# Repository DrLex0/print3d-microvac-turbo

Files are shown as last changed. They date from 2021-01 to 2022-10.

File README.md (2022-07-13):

# MicroVac Turbo
*A small (experimental) 3D printed handheld vacuum cleaner made from scrap parts*

### License
[Creative Commons - Attribution](https://creativecommons.org/licenses/by/4.0/)

### Gallery

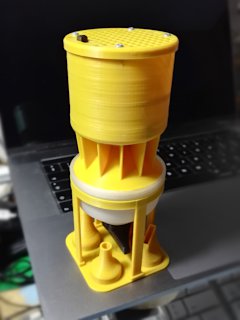
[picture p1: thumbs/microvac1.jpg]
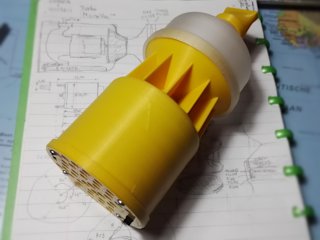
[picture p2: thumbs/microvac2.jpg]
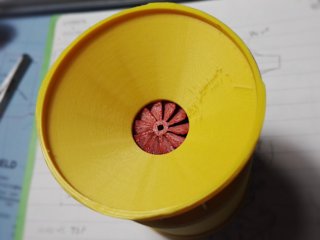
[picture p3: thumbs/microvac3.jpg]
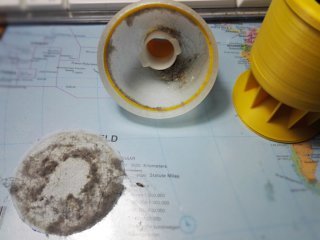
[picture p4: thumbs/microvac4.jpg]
Dirt
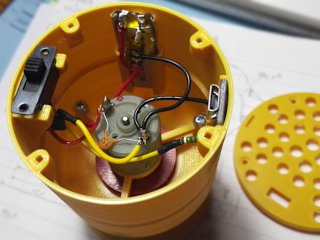
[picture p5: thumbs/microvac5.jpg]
Internals
[🔎](images/microvac1.jpg) [🔎](images/microvac2.jpg) [🔎](images/microvac3.jpg) [🔎](images/microvac4.jpg) [🔎](images/microvac5.jpg)

## Description and Instructions

This is a small (about 60 mm diameter and 150 mm tall) handheld vacuum cleaner that I basically made from scrap parts. It is more like a proof-of-concept and was designed to fit the parts I had, not to use commonly available components. It is unlikely you will be able to print and build this without first modifying the 3D models, because the motor I used may not be easy to find, and the LiPo battery I used certainly is not easy to find.

This mini vacuum cleaner is built around a turbo style impeller, just because I wanted to see how well it would work (pretty well apparently). After trying out a few impeller designs from other people, I created my own. This was done purely by eyeballing and wet-finger guessing, it probably isn't the most efficient design possible but it works pretty well for this application.

The vacuum cleaner itself is a very basic design, no fancy cyclones (if there is cyclone action, it would be by accident), just a widening collector to slow down the air and provide a relatively large filter area. I didn't expect much of it but it works surprisingly well and is useful for cleaning keyboards or electronic devices and hard to reach corners. It isn't ideal to suck up a lot of fluffy or very fine dust because this quickly clogs the filter, but it is great to quickly get rid of small pieces of junk. When sanding or carving something, I no longer care about the mess I make, I just vacuum it afterwards. It's also useful to clean the inside of a confined space like a 3D printer enclosure. This is one of the most useful 3D prints I have made so far.

Note: there is no relation between this freely available 3D printable model and any products or brands that may use the MicroVac name. This model is not condoned or endorsed by any company.

### Parts

IIRC the motor I used came from SparkFun long ago and they no longer sell this model at the time of this writing. The specifications were:
- 1.5V to 4.5V,
- 8400 rpm at 1.5V, 230 mA
- 14200 rpm at 3V, 280 mA
- 2 mm axle diameter
- Overall diameter: 20.75 mm, front diameter (around axle) 15.90 mm
- Coil impedance around 1 Ω

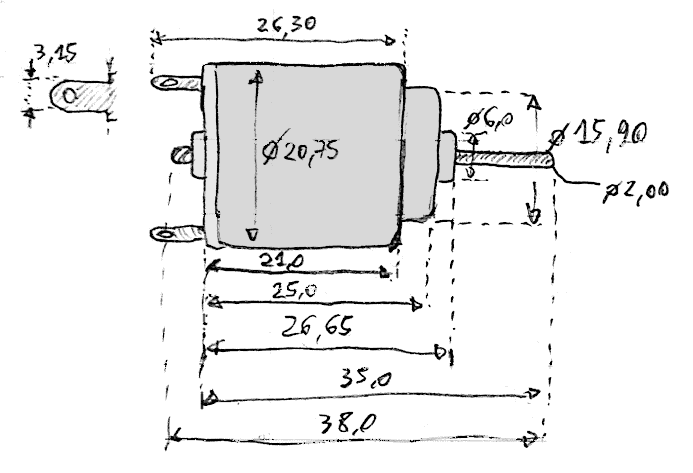
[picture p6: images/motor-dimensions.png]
Motor dimensions


It looks like this motor is a clone of the Mabuchi *RE-140RA.* You can get these clones from the usual sources like AliExpress. Those who live in Europe, the Reely R140 motor sold by Conrad (article 518398) is a perfect match.

My first motor endured almost 2 years of quite intensive use before its brushes were completely gone. Two things probably contributed to wear:
1. I hadn't sealed any of the holes in the housing, hence fine dust that got past my crude filter could enter the motor;
2. I added some oil to the bearings at regular intervals, to combat noise that was probably caused by the fine dust grinding away the bearings. I mostly added oil at the rear, because this was easily accessible (and actually also most prone to wear and causing noise). The oil mixed with the dust and became a grinding paste that lodged itself between the brushes and commutator, eventually destroying the brushes.

Learning from the above, the lifespan of the motor can probably be greatly improved by sealing all holes in the motor housing, and only applying minimal amounts of oil or (preferably) grease. Minimising vibrations by balancing the impeller will also help.\
I doubt whether genuine Mabuchis would last much longer. It makes sense to simply buy a stockpile of whatever you can get cheaply. Replacing the motor is easy, especially when using pluggable contacts.

Any motor with roughly similar specs and dimensions should be suitable. Pay attention to the RPM and current ratings. Lower values will not work well. Even if the free-air RPM matches, a motor with lower current draw will be too slow when it experiences the load of having to drive the impeller. After my original motor was beyond repair, I tried a purported Mabuchi (bought via AliExpress, so likely a fake) but it had a higher impedance on its coils and could not draw the same current, which made it too slow. I managed to transplant the rotor of the original motor into this new motor's housing and this works OK, although the commutator will probably fail next and then I will have to find a better replacement after all.

If you use a different model of motor, you will need to model your own motor mount. It may be a good idea to try a *drone motor* which will certainly be able to displace a lot of air. However, keep in mind that there will be an upper limit to the speed you can drive the impeller before it explodes into bits. Make sure to wear eye protection if you plan to find this speed limit… Also consider that the impeller will tend to spin faster inside the enclosure than in free air, especially when the inlet is obstructed.

The battery I used is a 220 mAh 551240 LiPo which came from a Chinese ‘spy pen’ gadget, the one [I reviewed here](https://www.dr-lex.be/hardware/spypen_review.html). After the protection circuit of this battery failed, I tried to find a replacement and this proved very difficult. This bare battery remained in my stockpile of loose parts until I decided to use it for this project, with a basic protection circuit attached to it. In other words, you will likely need to adapt the 3D model to fit a battery you can easily obtain. A slightly higher capacity than 220 mAh may be recommended although autonomy is pretty decent even with this small value. A bigger battery would also allow more current draw, hence better performance. You will of course need to modify the 3D model to allow mounting a different shape of battery.

The switch is a pretty standard 2P2T slide switch, a classic model that has been around for ages and should still be easy to find. I connected the two arrays of contacts together because the currents it has to deal with may be a little higher than it is intended for. So far, no problems whatsoever.

For the USB socket. I used a simple microUSB break-out board that is easy to find on AliExpress and the like, the dimensions are 14.1x12.7 mm. Of course you could use any other connector, USB-C if you want to be fancy. You could also look for a combination charge/discharge protection board that does everything to keep the battery in good shape and offers an indicator light.

The screws I used are simple self-tapping screws, 3 larger screws that hold the parts of the main body and the motor mount together are 2.9 mm × 9 mm; and 4 smaller screws for the lid are 2.2 mm × 6.5 mm. Anything similar will probably work, you could adjust the models if need be.

You also need some kind of *filter.* The 3D printed ‘filter’ is insufficient, its only purpose is to hold the actual finer filter in place. The filter should be a circle with 60 mm diameter, and it should be the thinnest possible material that still blocks fine dust. I simply peel and cut one layer from soft multi-ply toilet paper, which works very well.

### Printing

The recommended layer height for nearly all parts is 0.2 mm. Only the impeller should be printed at 0.1 mm layers with an extrusion width of 0.4 mm. For the other parts I recommend an extrusion width of 0.6 mm, which will be beneficial for strength. Since all parts are basically shells, infill doesn't really matter and safest is to use 100%.

I used PLA for all parts except the filter ring (see below) and the impeller, which is ABS. The only real reason for this is that I'm able to produce more detailed prints with ABS. Use whatever works best for you.

It is highly recommended to print the `FilterRing` in an *elastic filament* like TPU. Otherwise there may be a considerable air leak around the filter edges. Whether you need **one** or **two** of these filter rings, depends on how flat and smooth you can make the interface between the `CenterPart` and `Filter` parts. If it is perfectly flat, this interface will offer a good enough seal on its own, otherwise an extra gasket is recommended. In my case the surfaces are perfect because I print on a glass bed, but an alternative is to sand and polish these two surfaces.

The impeller is provided in both `clockwise` and `countercw` (counter-clockwise) variants. Which one you need, depends on the direction the axle of your motor turns when viewed from the front. The motors I have tried, all turn clockwise when connected with their indicated polarity. You could of course just swap the wires if you printed the wrong version, although I'm not sure whether some motors aren't optimised to run in a certain direction.\
There are 2 versions of the impeller, the `v2` version has blades of alternating height. It is hard to test this quantitatively, but in practice it appears to perform better.

There are two lid designs, `cheese` has a pattern with round holes, `grid` is a regular grid and in theory offers slightly better airflow.

Several mouthpiece styles are available. The most useful ones proved to be 3, 4, 5, and 6. These are press-fit, which means you might need to experiment a bit with scale factors to get a good fit. In my case, I have to scale these pieces to 99.5% in the XY plane to get a good fit. I printed the number 4 and 6 pieces in flexible PLA to reduce the risk of scratching things.

A stand is also provided that can hold up to 4 mouthpieces besides the vac itself. When printed well, the two parts will fit and hold together when pushed into each other, otherwise sandpaper and/or glue are your friends.

### Assembly

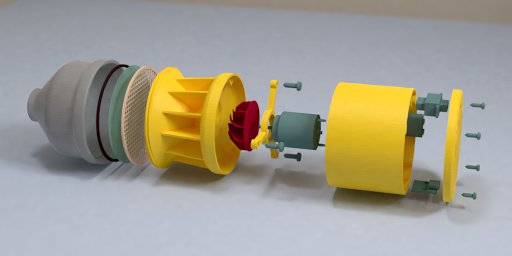
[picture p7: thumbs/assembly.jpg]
Exploded view
[🔎](images/assembly.jpg)

Assembly is rather straightforward. You should start by pushing the motor into its mount (it's press-fit) and then mounting the impeller. Tune the position of the impeller on the axle such that it just does not scrape against the intake part, also not when the airflow is blocked and the motor spins at its highest speed. I have created a spacer out of cardboard, fine-tuned with layers of adhesive tape through trial-and-error, such that I can simply push the impeller on the axle with the ideal spacing right away. When this is OK, assemble the other parts.

Cut a fine 60 mm diameter filter out of some thin material, like a single ply of soft toilet paper. You can use the coarse filter as a template. Place this thin filter on top of the coarse filter, preferably at the top side where the grid is slightly recessed. Then place the flexible ring on top of the fine filter and align everything. While keeping the set of filters in this orientation, insert them into the collector with its outlet pointing upwards. If you decided to use two flexible rings, place the second ring onto the coarse filter. Then screw the collector onto the main body of the vacuum cleaner.

The inlet has a tab on the side, the idea was to stick a piece of paper or plastic sheet to it, to act as a valve. This has proven unnecessary though when emptying the collector regularly. Junk will typically move to the sides and not fall back into the inlet unless too much has been collected.

Due to imperfections of the 3D printing process, the impeller may be unbalanced enough that it causes annoying vibrations. Balancing the impeller is fairly easy: mount it on a perfectly straight 2 mm rod (like a drill bit), and let the axle roll on 2 ‘rails’ that are perfectly level and flat. If well balanced, the impeller should not seek out a specific orientation when nudged. If it does, first look for obvious blobs at the side that likes to point downwards, and remove them. If this does not suffice, stick some adhesive tape at the edge that likes to point upwards, and try to dose it such that the impeller no longer has any preferred position. Enjoy your vibration-free MicroVac!

#### Wiring

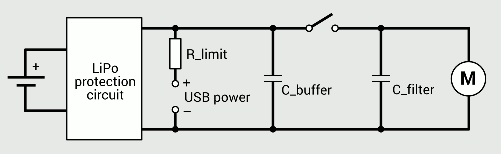
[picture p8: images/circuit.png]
circuit


How to wire this thing will depend on the specific parts used, but in general it is rather straightforward. One wire of the motor goes to common ground, the other goes through a switch to the positive terminal of the battery protection circuit. The positive terminal of the battery's over-voltage protection circuit goes to a charging port. Ideally there should also be a current regulator to limit the current during charging. Usually, a good rule of thumb for the charge current is the same milli-amperes value as the battery's capacity in mAh (or “1 C”). In my case, the current limiter is extremely simple: a resistor chosen such that the peak current is not much higher than 1 C. This is inefficient, but OK given the small capacity of the battery I'm using and the low current it charges at. For a higher capacity battery, you will want to use some active charging circuit, because a resistor could become dangerously hot.

There are some ready-to-use boards that have a microUSB (or nowadays USB-C) port with charge and protection circuit all-in, but you will need to modify the 3D models to fit those.

If you cannot find a motor that runs at a good speed between 3.8 and 4.2 V, you will have to add some kind of booster circuit, or use 2 batteries with possibly a step-down circuit.

Refinements that are good practice: ensure there is a small ceramic capacitor as close to the motor terminals as possible, to filter out noise (may not be needed depending on the type of motor). Also, a decently sized capacitor across the battery (I used 470 nF), to buffer the initial inrush current when switching on the motor. This should also be placed as near to the motor as possible but must come before the switch. Without this capacitor, the protection circuit of my battery would sometimes engage because the inrush current could be high enough for the protection circuit to consider it a short-circuit.

Using crimp terminals for the motor will make it easier to replace than when soldering it. The RE-140RA and clones have tabs that accept plain flat 2.8 mm terminal connectors. Ideally the connectors should be for 0.3 mm thick tabs but if hard to find, 0.5 mm connectors will also work after some careful squishing.

### Using

There isn't much to say about how to vacuum things, just turn it on and go for it. If you didn't make a valve to keep dirt inside, the only thing you should avoid is wildly shaking the device or allowing it to fill up to a point where dirt can no longer stay inside.

Depending on your wiring, you may be able to get an extra boost by connecting the USB cable. In my case the gain is minimal due to the rather high impedance of my barebones current limiter. Make sure you cannot send the motor into explosive overdrive when it receives 5 V instead of the usual 4.2 V maximum of a LiPo battery.

To empty the reservoir, unscrew the collector from the rest, obviously while keeping it upright. Then either take out the filters using tweezers, or just immediately topple the whole thing over above a dustbin, catching the filters with your hand. If you're careful, you can shake the fine filter and reuse it, but the effort to make new filters is pretty small anyway. Afterwards, reassemble according to the above instructions.

The mounting/removing of the filters and the screw thread connection to mount the collector aren't very user-friendly, but this was only a proof-of-concept after all.

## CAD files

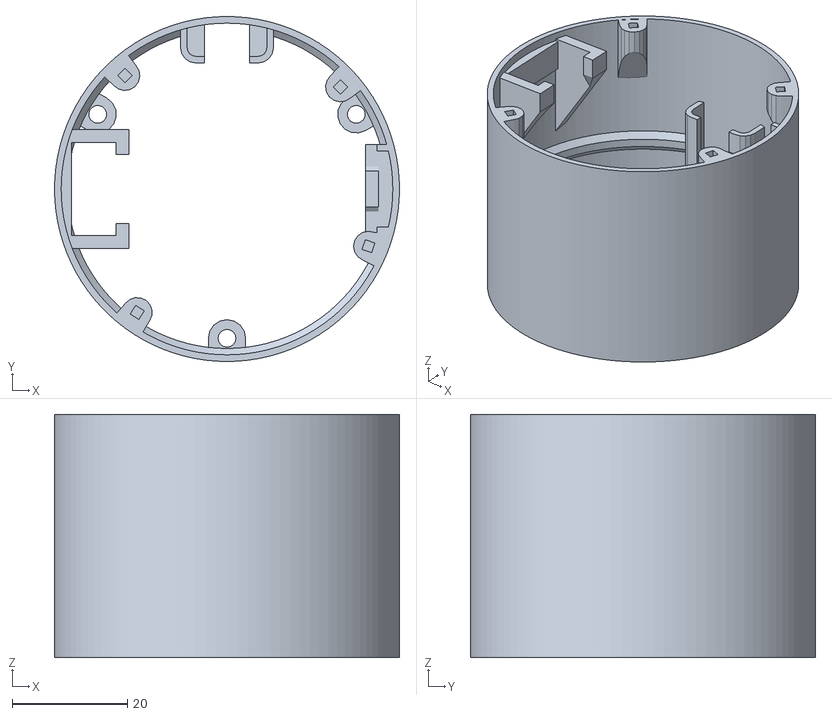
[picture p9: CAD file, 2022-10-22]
stl_files/UpperPart.stl
60.0 x 60.0 x 42.3

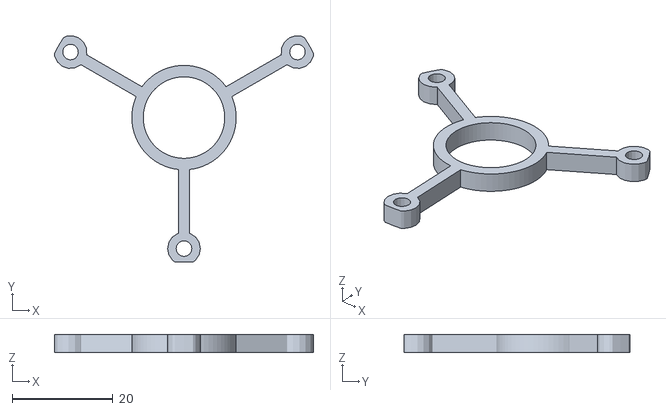
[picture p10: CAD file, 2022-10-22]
stl_files/MotorMount.stl
51.3 x 44.9 x 3.60

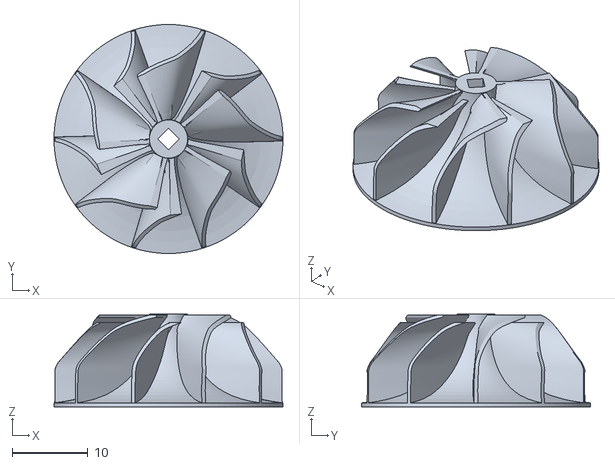
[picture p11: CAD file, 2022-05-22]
stl_files/Impeller-v2-countercw.stl
30.2 x 30.2 x 12.2

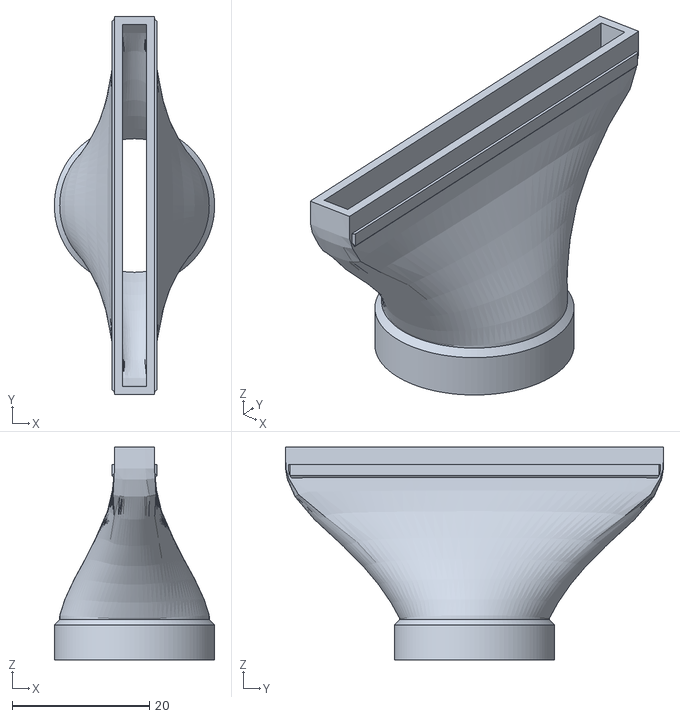
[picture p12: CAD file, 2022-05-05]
stl_files/Mouthpiece6.stl
23.3 x 55.0 x 30.9

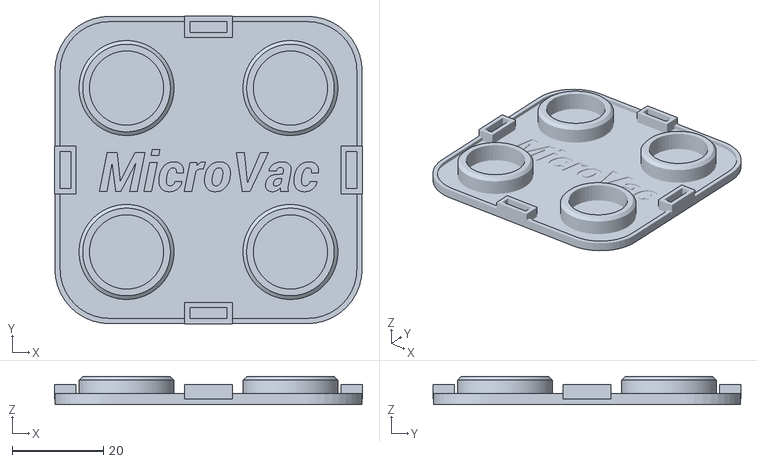
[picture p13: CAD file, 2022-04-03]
stl_files/Stand-lower.stl
67.6 x 67.6 x 6.20

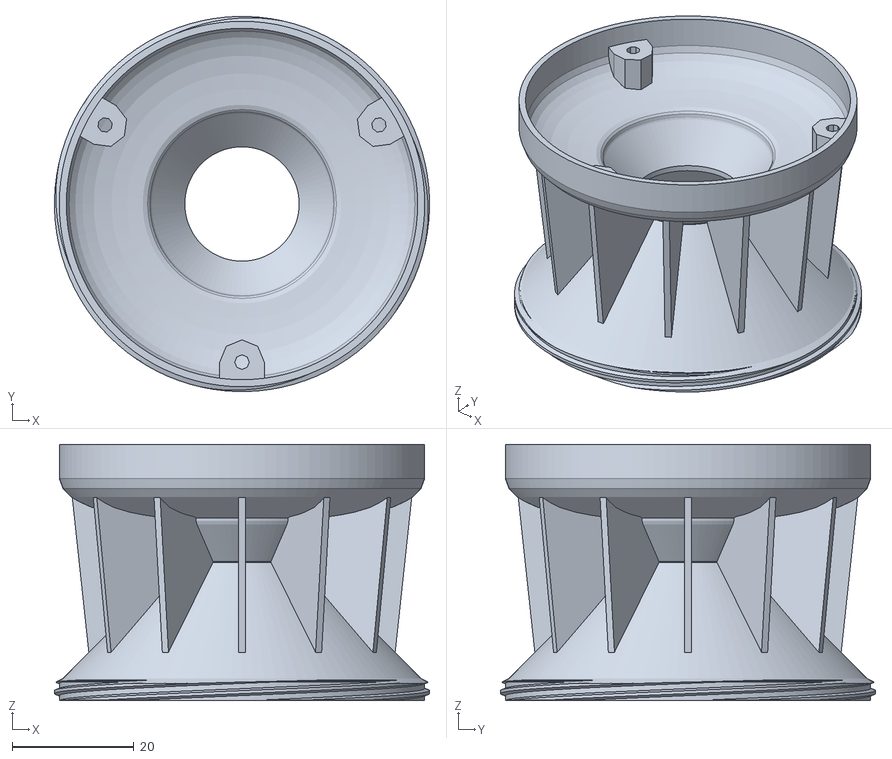
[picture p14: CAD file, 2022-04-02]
stl_files/CenterPart.stl
61.6 x 61.6 x 42.0

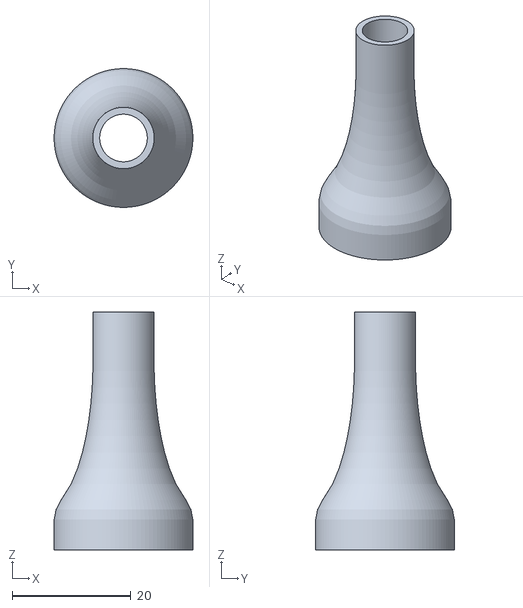
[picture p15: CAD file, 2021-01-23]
stl_files/Mouthpiece5.stl
23.3 x 23.3 x 40.0

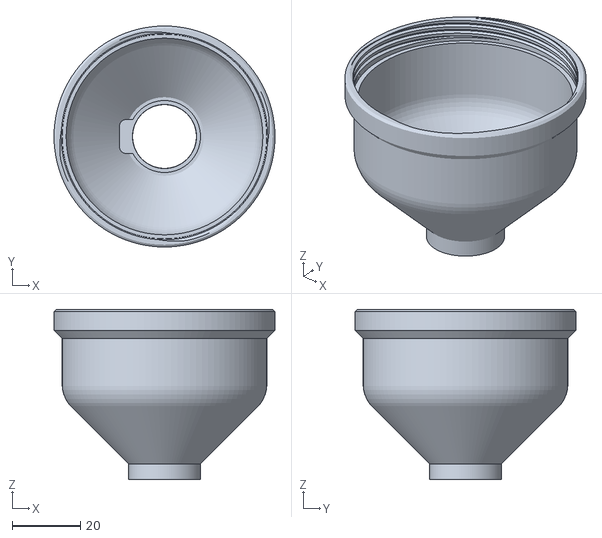
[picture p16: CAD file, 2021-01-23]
stl_files/Collector.stl
64.8 x 64.8 x 49.9

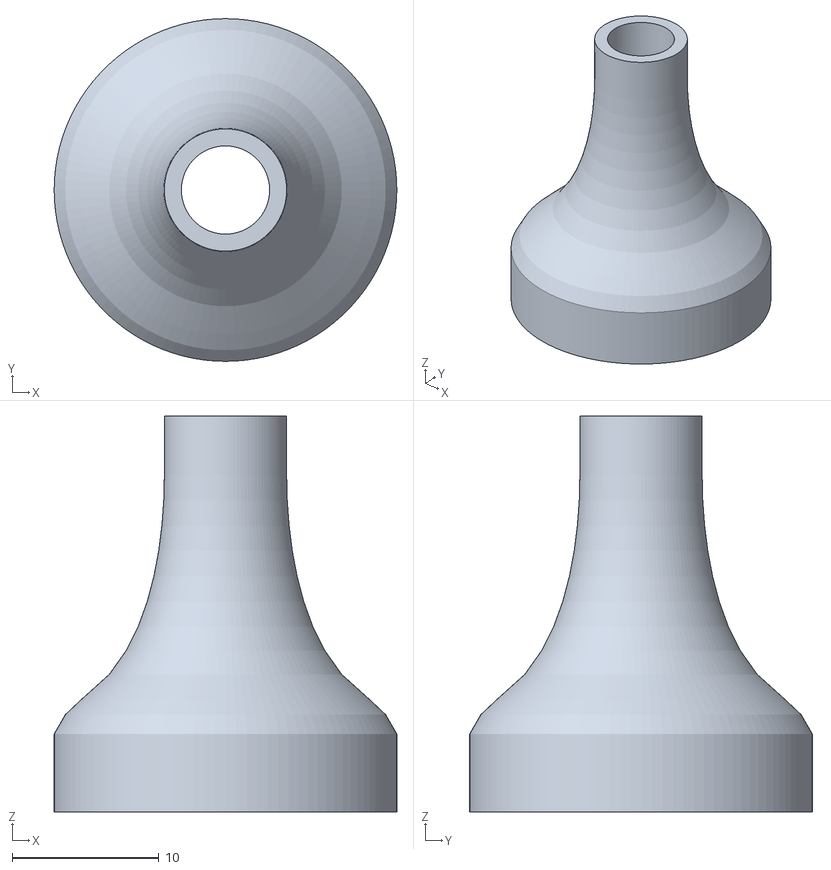
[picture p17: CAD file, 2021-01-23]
stl_files/Mouthpiece3.stl
23.3 x 23.3 x 26.9

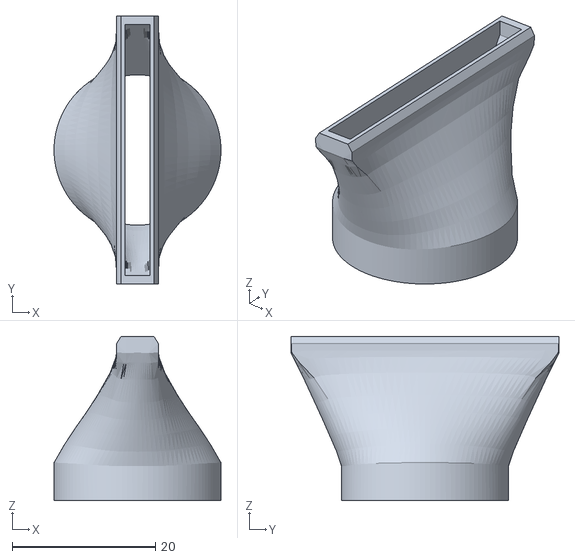
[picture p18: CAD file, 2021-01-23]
stl_files/Mouthpiece4.stl
23.3 x 37.4 x 22.9

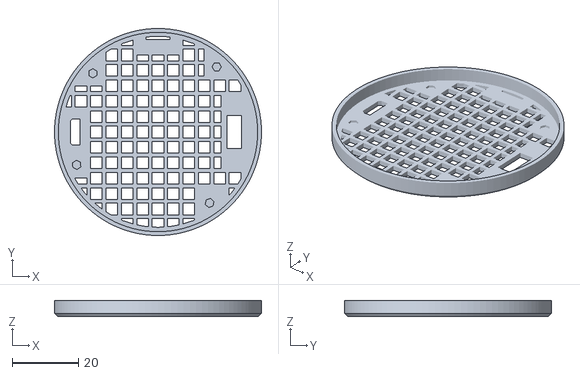
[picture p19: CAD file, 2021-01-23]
stl_files/Lid-grid.stl
62.6 x 62.6 x 4.90

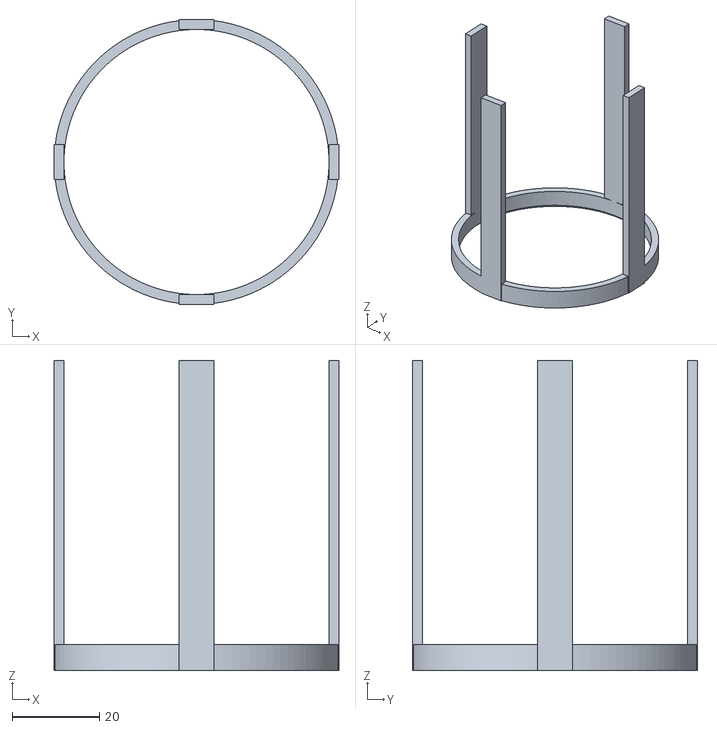
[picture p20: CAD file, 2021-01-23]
stl_files/Stand-upper.stl
65.2 x 65.2 x 70.9

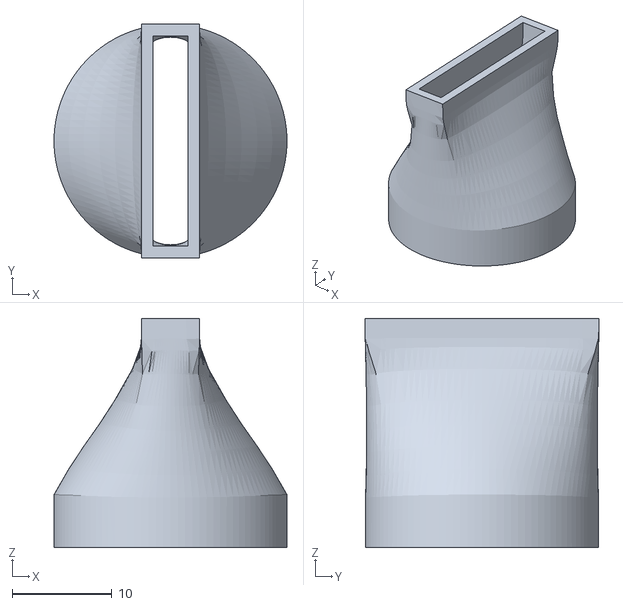
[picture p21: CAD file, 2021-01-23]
stl_files/Mouthpiece2.stl
23.3 x 23.4 x 22.9

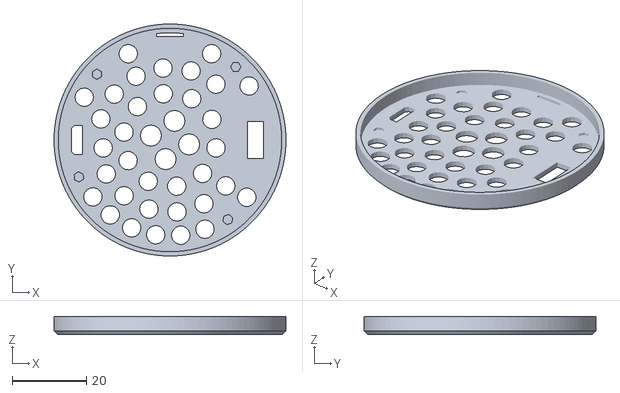
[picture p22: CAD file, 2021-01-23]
stl_files/Lid-cheese.stl
62.6 x 62.6 x 4.90

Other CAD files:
stl_files/Impeller-v2-clockwise.stl
stl_files/Mouthpiece1.stl
stl_files/FilterRing.stl
stl_files/Filter.stl
MicroVac-mouths.blend
MicroVac-stand.blend
stl_files/Impeller-v1-clockwise.stl
stl_files/Impeller-v1-countercw.stl

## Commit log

2021-01-23 Create repository
    [CenterPart.stl, Collector.stl, Filter.stl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]
2021-01-23 Reorganise files
    [CenterPart.stl, Collector.stl, Filter.stl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]
2021-01-30 Mention screw sizes
2022-03-23 Add extra wide mouthpiece; split off mouthpieces to separate Blender file
    [MicroVac-mouths.blend, Mouthpiece6.stl]
2022-03-23 Add more info about motor
2022-04-02 Make center part screw holes beefier
    [CenterPart.stl]
2022-04-03 Improve stand.
    - Slightly tighter fit on mouthpiece holders
    - Extra ridge for extra style
    [MicroVac-stand.blend, Stand-lower.stl]
2022-05-05 Improve mouthpiece 6 design
    [MicroVac-mouths.blend, Mouthpiece6.stl]
2022-05-22 Make motor mount stronger
    [MotorMount.stl]
2022-05-22 Rename impeller STLs
    [Impeller-v1-clockwise.stl, Impeller-v1-countercw.stl]
2022-05-22 Add v2 alternative impeller.
    v2 has 2 stages of blade height, which might offer better performance.
    Did some tweaking to the shape to encourage slicers to produce a cleaner print (retro-actively applied to v1).
    Also made the blend file more efficient through use of the array modifier and reducing unnecessary detail.
    Add some extra hints to the README.
    [Impeller-v1-clockwise.stl, Impeller-v1-countercw.stl, Impeller-v2-clockwise.stl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]
2022-10-22 Tweaks to motor mount and upper part
    [MotorMount.stl, UpperPart.stl]
